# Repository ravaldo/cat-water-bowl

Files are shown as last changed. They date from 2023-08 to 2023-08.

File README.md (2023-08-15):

# Auto-filling pet water bowl

As a (former) cat owner for many years, this project arose from of my increasing dislike with the time it took to clean and maintain the pet [drinking fountain](https://i.imgur.com/fLEMcdn.jpg) I had. I wanted to return to a standard water bowl again and have it automatically filled with water:
* quick to clean
* no need to purchase filters
* smaller volumes of water meant fewer worries of water stagnating
* push notifications sent to my phone
  
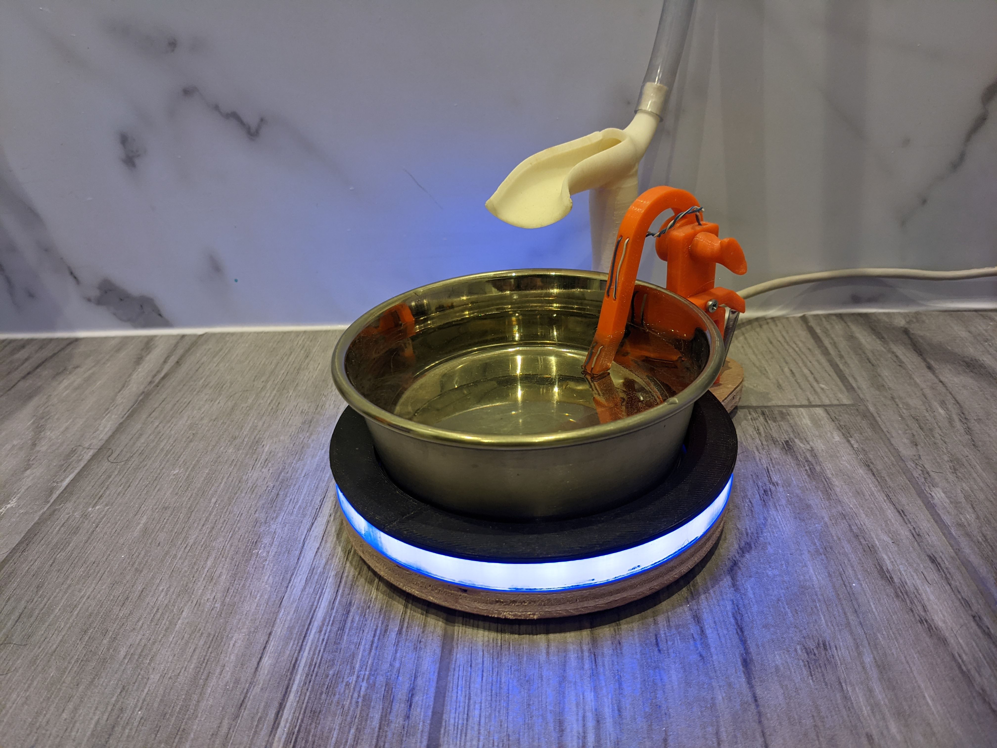
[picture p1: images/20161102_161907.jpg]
3d printed


## CAD / 3d Printing
The Fusion 360 file is included. I printed the spout in ABS in three parts so I could solvent weld them together and then vapour smooth them to be water proof. The light ring was printed in a transparent PLA. While the base could be printed (assuming your print bed is large enough) I opted to make it out of plywood and a 1:1 paper template is included.

## Hardware
|quantity|parts|
|:-:|-|
|1|Arduino Nano|
|2|NRF24L01|
|1|N-Channel Mosfet (SUP75N06-08)|
|1|Flyback Diode (1N4004)|
|3|NPN Transistors (BC548)|
|1|5V Voltage Regulator (LD117AV50)|
|1|3.3V Voltage Regulator (LD117AV33)|
|1|12V RGB LED strip segment|
|6|capacitors|
|6|resistors|
|2|RJ45 breakout boards or keystone jacks|
|1|DC Barrel Jack|
|1|12V Power Supply|
|1|12V Solenoid Valve (!NORMALLY CLOSED!)|
|1|15mm equal isolating tee|
|1|15mm x 1/4" compression straight adaptor|
|1|10mm barbed fitting to 1/4" BSP|
|1m|3/8" ID, 1/2" OD Hose|
|1|small tension spring|
|2|M5 nuts
|2|M5 pan head screws

It's worth mentioning that I made this project around 2012 which is why the NRF24L01 module is used for communication (the first ESP8266 was released a few years later). If I were redeploying this again today I would opt for a single ESP32 board and set it up for [MQTT](https://mqtt.org/).

Like most UK bathrooms I didn't have a convenient socket nearby, so, while the fountain resided next to my bathroom sink (plumbed into the cold water line), the circuit and power supply were in an adjacent room; the fountain was connected by an ethernet cable (hence the RJ45 adapters) and the solenoid valve was connected using 2 core speaker wire.

## Code
The arduino sketch is set up as a [finite-state machine](https://en.wikipedia.org/wiki/Finite-state_machine) with two primary inputs; one to detect if the bowl is present and another to detect if the bowl contains water. Two secondary inputs are available for setup and testing; one allows to you set the "water filling time" at the fountain and the other is used to test connectivity between the NRF24 modules.

Short demo video [HERE](https://youtu.be/1sBqBGg-HPs).

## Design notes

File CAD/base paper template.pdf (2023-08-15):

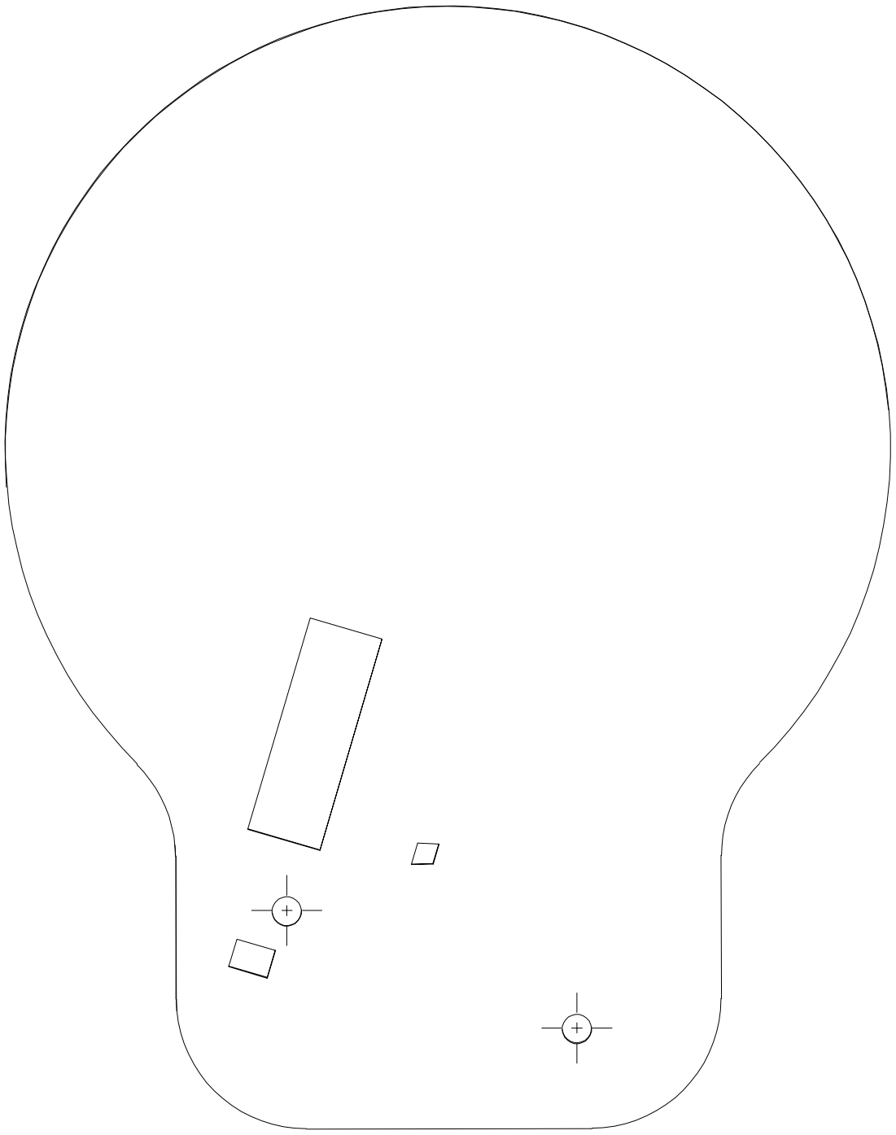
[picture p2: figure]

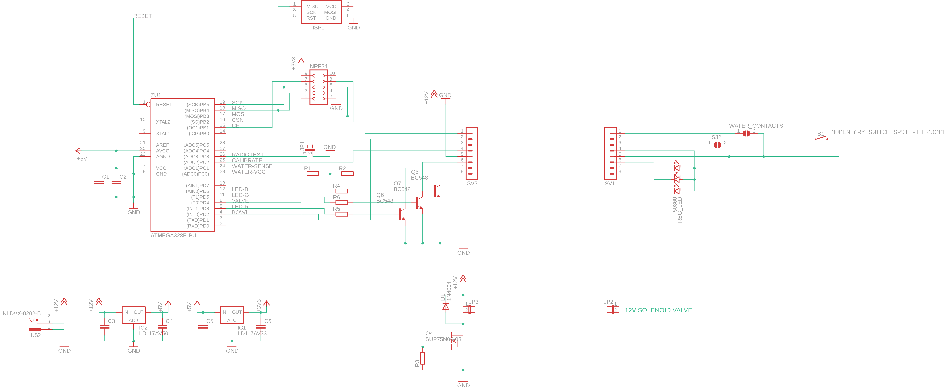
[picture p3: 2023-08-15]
circuit/schematic.png

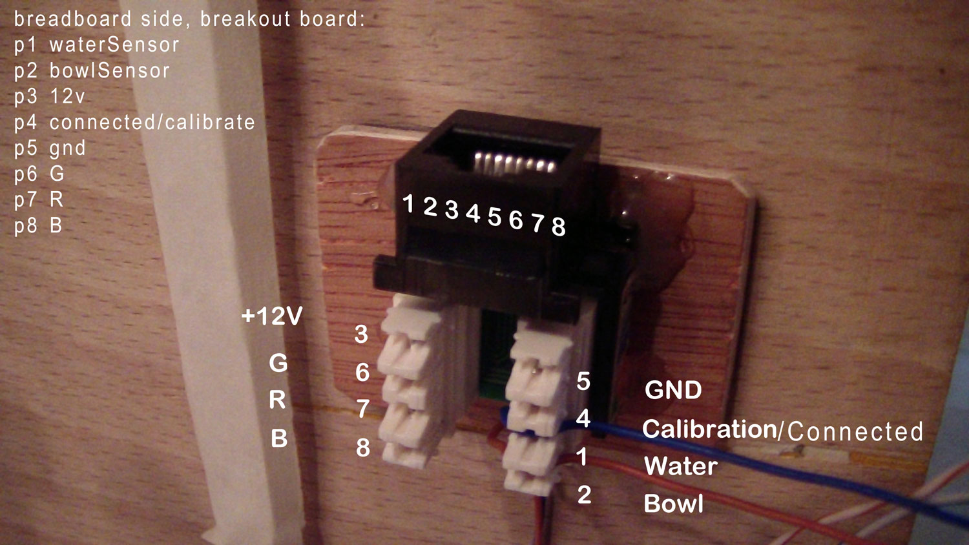
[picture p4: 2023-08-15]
circuit/ethernet pinout.jpg

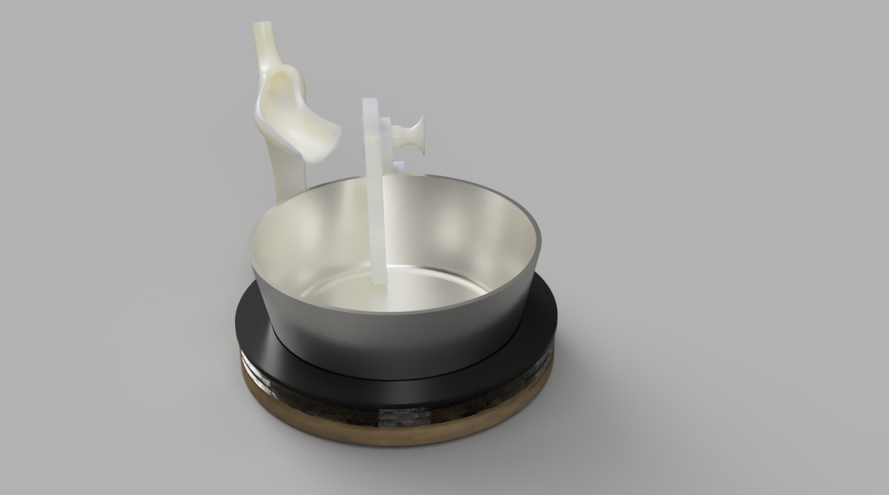
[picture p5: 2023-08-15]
CAD/render.png

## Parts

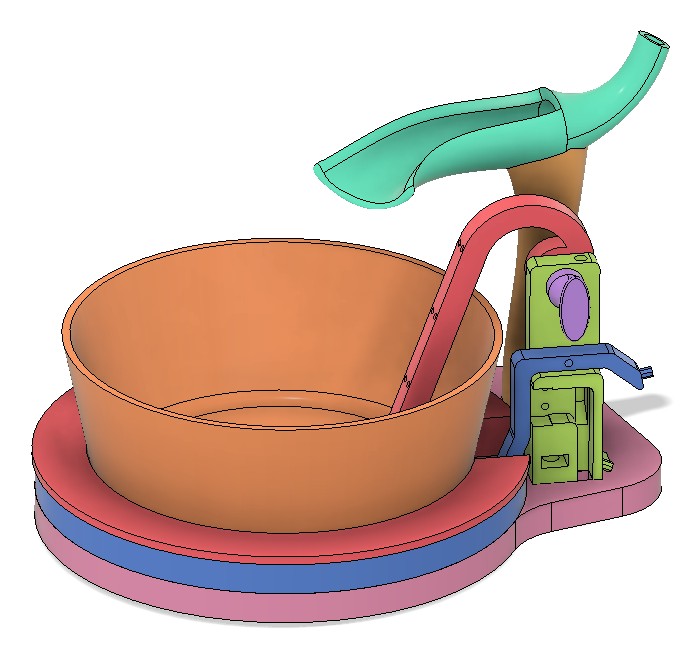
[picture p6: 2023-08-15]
CAD/component view.jpg

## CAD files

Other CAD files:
CAD/water bowl.f3d

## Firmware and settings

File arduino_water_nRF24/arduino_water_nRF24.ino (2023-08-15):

#include <SPI.h>
#include "RF24.h"
#include "RF24Network.h"
#include "my_vars.h"

////////////////////////////////////////////

#define secs *1000UL
#define mins *60 secs
#define hrs *60 mins

unsigned long bowlWait = 5 mins;          // time to wait for bowl to return
unsigned long evaporationWait = 25 mins;  // time to wait for water to evaporate before filling
unsigned long waterSampleWait = 5 mins;   // duration between taking water samples
unsigned long waterFillingTime = 25 secs; // changed in CALIBRATING mode
const unsigned long maxTimeOn = 30 secs;  // max time the valve will be on in a single WATERFILLING event
const unsigned long minTimeOn = 10 secs;  // min time the valve will be on in a single WATERFILLING event
const unsigned long expFillGap = 6 hrs;   // min 6hrs expected between fills, for warning purposes
const unsigned long debugPrintWait = 1 secs;   // time to wait to output debug msgs
const unsigned long armLoweringWait = 10 secs; // time to wait for sensor arm to be lowered

const int ledR = 7;
const int ledG = 5;
const int ledB = 6;
const int bowlSensor = 2; // INT0 is pin2
const int valve = 4;
const int waterVcc = A0;
const int waterSensor = A1;
const int calibrationPin = A2;
const int radioTestPin = A3;
const int connectedLed = A4;
const int connectedPin = 3;
const int debugSelect = 8;
const int CE = 9;
const int CSN = 10;
// unused pins A5, A6, A7
// nano PWM pins: 3, 5, 6, 9, 10, 11
// nRF24L01 set up on the nano's SPI bus... 9-CE, 10-CSN, 11-MO, 12-MI, 13-SCK

const char msg_FOUNTAINRESET[] = "fountain reset";
const char msg_READY[] = "fountain ready";
const char msg_BOWLREMOVED[] = "bowl removed";
const char msg_BOWLMISSING[] = "bowl missing > 5mins";
const char msg_BOWLREPLACED[] = "bowl replaced";
const char msg_BOWLEMPTY[] = "bowl empty";
const char msg_FILLED[] = "bowl filled";
const char msg_FILLEDTOOSOON[] = "filled again too soon";
const char msg_CHECKWATERSENSOR[] = "check water sensor";
const char msg_CALIBRATED[] = "fill time calibrated";
const char msg_RADIOTEST[] = "radio test";
const char msg_DISCONNECTED[] = "fountain disconnected";
const char msg_CONNECTED[] = "fountain connected";

boolean msgDisconnectedSent = false;
boolean msgRemovedSent = false;
boolean msgMissingSent = false;
boolean msgFilledTooSoonSent = false;
boolean msgErrorSent = false;

volatile State state;
volatile unsigned long timeStamp = 0;     
volatile unsigned long lastInterrupt = 0;
volatile int countInterrupts = 0;
unsigned long lastFillTime = 0;           // time since the bowl was last filled
unsigned long lastWaterSampleTime = 0;    // time since the water was last sampled
unsigned long lastDebugOutput = 0;        // time since the debug msg was last printed

const int nodeID = 1;  // unique nodes required for each project
RF24 radio(CE,CSN);
RF24Network network(radio);

////////////////////////////////////////////

void setup() {
  Serial.begin(57600);
  Serial.println("System started");

  SPI.begin();
  radio.begin();
  network.begin(90, nodeID);

  delay(100);
  pinMode(valve, OUTPUT);
  pinMode(waterVcc, OUTPUT);
  digitalWrite(valve, LOW); // make sure valve is off
  digitalWrite(waterVcc, LOW);

  pinMode(ledR, OUTPUT);
  pinMode(ledG, OUTPUT);
  pinMode(ledB, OUTPUT);
  pinMode(connectedLed, OUTPUT);
  pinMode(connectedPin, INPUT_PULLUP);
  pinMode(calibrationPin, INPUT_PULLUP);
  pinMode(bowlSensor, INPUT_PULLUP);
  pinMode(radioTestPin, INPUT_PULLUP);
  pinMode(debugSelect, INPUT_PULLUP);
  pinMode(waterSensor, INPUT); // using external 1Mohm pullup

  attachInterrupt(0, whereIsMyBowl, CHANGE); // INT0 is pin2
  attachInterrupt(1, whereIsMyBowl, CHANGE); // INT1 is pin3
  
  transmit(msg_FOUNTAINRESET, sizeof(msg_FOUNTAINRESET));
  digitalWrite(connectedLed, HIGH);
  if (!isFountainConnected() || !isBowlPresent())
    whereIsMyBowl();
  else                   // could just set it to start from DISCONNECTED
    setState(ARMWAIT);   // but doing this avoids the extra prints & emails being sent
  Serial.println("Setup finished");
}

////////////////////////////////////////////

void loop() {
  
  if (digitalRead(debugSelect) == LOW) {
    if (uint32_t(millis() - lastDebugOutput) > debugPrintWait)
      printStatus(); // particularly handy to check the waterSensor sensitivity
  }

  switch(state) {

    case DISCONNECTED: {
      setColour(BLACK);
      digitalWrite(valve, LOW);
      digitalWrite(waterVcc, LOW);
      digitalWrite(connectedLed, LOW);
      if (!msgDisconnectedSent) { // limit msgs to one per event
          transmit(msg_DISCONNECTED, sizeof(msg_DISCONNECTED));
          msgDisconnectedSent = true;
      }
      if (isFountainConnected()) {
        delay(100); // guard against accidental presses
        if (isFountainConnected) { // fountain definitely reconnected
          transmit(msg_CONNECTED, sizeof(msg_CONNECTED));
          msgDisconnectedSent = false; // reset
          digitalWrite(connectedLed, HIGH);
          setState(BOWLMISSING);
        }
      }
      break;
    }    
    
    case BOWLMISSING: {
      digitalWrite(valve, LOW);
      digitalWrite(waterVcc, LOW);
      unsigned long elapsedTime = millis() - timeStamp;
      if (elapsedTime <= bowlWait) {
        setColour(YELLOW);
        if (!msgRemovedSent) { // limit msgs to one per event
          transmit(msg_BOWLREMOVED, sizeof(msg_BOWLREMOVED));
          msgRemovedSent = true;
        }
      }
      if (elapsedTime > bowlWait) {
        setColour(RED);
        if (!msgMissingSent) { // limit msgs to one per event
          transmit(msg_BOWLMISSING, sizeof(msg_BOWLMISSING));
          msgMissingSent = true;
        }
      }
      if (isBowlPresent()) {
        delay(100); // guard against accidental presses
        if (isBowlPresent()) { // bowl definitely back
          transmit(msg_BOWLREPLACED, sizeof(msg_BOWLREPLACED));
          msgRemovedSent = false; // reset
          msgMissingSent = false; // reset
          setState(ARMWAIT);
        }
      }
      break;
    }

    case ARMWAIT: {
      // the bowl has just been replaced and it's likely empty...
      // lets not wait for evaporationWait, instead
      // wait X seconds to allow the arm to be lowered and then check water level
      setColour(WHITE);
      if (uint32_t(millis() - timeStamp) > armLoweringWait) {
        if (isWaterEmpty() && isBowlPresent()) {
          transmit(msg_BOWLEMPTY, sizeof(msg_BOWLEMPTY));
          setState(WATERFILLING);
        }
        else {
          transmit(msg_READY, sizeof(msg_READY));
          setState(READY);
        }
      }
      break;
    }
    
    case WATEREMPTY: {
      setColour(MAGENTA);
      if (!isWaterEmpty()) {
        transmit(msg_READY, sizeof(msg_READY));
        setState(READY);
        break;
      }
      if (uint32_t(millis() - lastFillTime) < expFillGap) {
        if (!msgFilledTooSoonSent) { // limit msgs to one per event
          transmit(msg_FILLEDTOOSOON, sizeof(msg_FILLEDTOOSOON));
          msgFilledTooSoonSent = true;
        }
      }
      if (uint32_t(millis() - timeStamp) >= evaporationWait) {
        msgFilledTooSoonSent = false; // reset
        setState(WATERFILLING);
      }
      break;
    }
    
    case WATERFILLING: {
      setColour(CYAN);
      if (uint32_t(millis() - timeStamp) < waterFillingTime)
        digitalWrite(valve, HIGH);
      else {
        digitalWrite(valve, LOW);
        lastFillTime = millis();
        timeStamp = millis();
        transmit(msg_FILLED, sizeof(msg_FILLED));
        if (isWaterEmpty())  // check the sensor is picking up the fresh water
          setState(ERRORS);
        else {
          transmit(msg_READY, sizeof(msg_READY));;
          setState(READY);
        }
      }
      break;
    }
    
    case CALIBRATING: {
      setColour(GREEN);
      digitalWrite(valve, HIGH);
      unsigned long elapsedTime = millis() - timeStamp;
      if (digitalRead(calibrationPin)) {    // if pin gone back to high
        delay(100);
        if (digitalRead(calibrationPin)) {  // debounce
          waterFillingTime = elapsedTime;
          if (elapsedTime > maxTimeOn)      // ensure we can't set it to overfill
            waterFillingTime = maxTimeOn;        
          if (elapsedTime < minTimeOn)      // ensure we can't set it too small
              waterFillingTime = minTimeOn;
          digitalWrite(valve, LOW);
          lastFillTime = millis();
          transmit(msg_CALIBRATED, sizeof(msg_CALIBRATED));
          setState(READY);
        }
      }
      break;
    }
    
    case RADIOTEST: {
      if (!transmit(msg_RADIOTEST, sizeof(msg_RADIOTEST))) {
        setColour(ORANGE);
        delay(500);
        setColour(PURPLE);
        delay(500);
      }
      else {
        setColour(ORANGE);
        delay(500);
        setColour(GREEN);
        delay(500);
      }
      if (digitalRead(radioTestPin)) // pin gone back to high
        state = READY; // set it directly so it doesn't print or reset the timestamp
      break;
    }
    
    case READY: {
      digitalWrite(valve, LOW);
      digitalWrite(waterVcc, LOW);
      setColour(BLUE);
      if (!isFountainConnected()) {
        Serial.println("  -- WE CAUGHT A DISCONNECTED EVENT NOT USING THE INTERRUPT.");
        setState(DISCONNECTED);
        break;
      }
      if (!isBowlPresent()) {
        Serial.println("  -- WE CAUGHT A BOWLMISSING EVENT NOT USING THE INTERRUPT.");
        setState(BOWLMISSING);
        break;
      }
      if (isCalibrating()) {
        setState(CALIBRATING);
        break;
      }
      if (isRadioTesting()) {
        state = RADIOTEST; // set it directly so it doesn't print or reset the timestamp
        break;
      }
      if (uint32_t(millis() - lastWaterSampleTime) > waterSampleWait) {
        lastWaterSampleTime = millis();
        if (isWaterEmpty()) {
          transmit(msg_BOWLEMPTY, sizeof(msg_BOWLEMPTY));
          setState(WATEREMPTY);
          break;
        }
      }
      break;
    }
    
    case ERRORS: {
      if (!msgErrorSent) {
        detachInterrupt(0);
        detachInterrupt(1);
        transmit(msg_CHECKWATERSENSOR, sizeof(msg_CHECKWATERSENSOR));
        msgErrorSent = true;
      }
      delay(500);
      setColour(RED);
      delay(500);
      setColour(BLACK);
      // reaching this state indicates the water was filled and the sensor didn't pick it up
      // possible cause 1; the water sensor was left raised up
      // possible cause 2; the water sensor wires have corroded and need replaced
      // need to reset the power if we reach this state
    }
    
    default:
      break;
  }// end of switch
}// end of loop

// interrupt routine
void whereIsMyBowl() {
  digitalWrite(valve, LOW);
  digitalWrite(waterVcc, LOW);
  
  if ((millis() - lastInterrupt) > 100) {
    if (!isFountainConnected())
      state = DISCONNECTED;
    else
      state = BOWLMISSING;

    timeStamp = millis();
    lastInterrupt = millis();
    countInterrupts++;
  }  
  // putting in the debounce logic has the effect of reducing multiple triggering
  // but the valve output isn't always forced to low as we would expect
  // therefore; copied the digitalWrites up to the switch case which ensures they are turned off
  // ... left them in this function anyway since it can't hurt
}

void setState(State s) {
  state = s;
  timeStamp = millis();
  printStatus();
}

////////////////////////////////////////////

boolean isBowlPresent() {
  return digitalRead(bowlSensor) == LOW ? true : false;
  // bowl pin pulled high by default
  // bowl switch is wired "normally open"
  // when bowl is present; switch is made; pin is low
  // when bowl is removed; switch is broken; pin is high
}

boolean isFountainConnected() {
  return digitalRead(connectedPin) == LOW ? true : false;
}

boolean isWaterEmpty() {
  int sample = getWaterSample();
  return sample < 150 ? false : true;
  // water pin pulled high temporarily using another outout pin and external resistor
  // water present; line is shorted; pin is pulled towards ground
}

boolean isCalibrating() {
  return digitalRead(calibrationPin) == LOW ? true : false;
}

boolean isRadioTesting() {
  return digitalRead(radioTestPin) == LOW ? true : false;
}

int getWaterSample(){
  digitalWrite(waterVcc, HIGH);
  delay(5);
  int sensorValue = analogRead(waterSensor);
  delay(5);
  digitalWrite(waterVcc, LOW);
  return sensorValue;
}

void setColour(const int colour[]){
  analogWrite(ledR, colour[0]);
  analogWrite(ledG, colour[1]);
  analogWrite(ledB, colour[2]);
}

void printStatus() {
  lastDebugOutput = millis();
  Serial.print("state: ");
  switch(state) {
    case BOWLMISSING:   Serial.print("BOWLMISSING"); break;
    case WATEREMPTY:    Serial.print("WATEREMPTY"); break;
    case WATERFILLING:  Serial.print("WATERFILLING"); break;
    case ARMWAIT:       Serial.print("ARMWAIT"); break;
    case READY:         Serial.print("READY"); break;
    case CALIBRATING:   Serial.print("CALIBRATING"); break;
    case RADIOTEST:     Serial.print("RADIOTEST"); break;
    case DISCONNECTED:  Serial.print("DISCONNECTED"); break;
    case ERRORS:        Serial.print("ERRORS"); break;
  }
  Serial.print("  ||  waterSensor: ");
  Serial.print(getWaterSample(), DEC);
  Serial.print("  ||  waterFillingTime: ");
  Serial.print(waterFillingTime, DEC);
  Serial.print("  ||  lastFillTime: ");
  Serial.print(lastFillTime, DEC);
  Serial.print("  ||  interrupts: ");
  Serial.print(countInterrupts, DEC);
  Serial.print("  ||  bowlSensor: ");
  Serial.print(digitalRead(bowlSensor));
  Serial.print("  ||  connectedPin: ");
  Serial.print(digitalRead(connectedPin));
  Serial.print("  ||  timeStamp: ");
  Serial.println(timeStamp, DEC);
}

bool transmit(const char msg[], int msgsize) {
  network.update();
  RF24NetworkHeader header(0, 'W');
  
  int count = 1;
  bool ok = false;
  while (count <= 3 && !ok) {
    Serial.print("Sending: ");
    Serial.print(msg);
    ok = network.write(header, msg, msgsize);
    if (ok)
      Serial.println(" ... successfull! ");
    else
      Serial.println(" ... failed!");
    count++;
  }
  return ok;
}

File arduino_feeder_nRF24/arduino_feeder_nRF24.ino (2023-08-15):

#include <SPI.h>
#include "HX711.h"
#include "RF24.h"
#include "RF24Network.h"

#define secs *1000UL
#define mins *60 secs
#define hrs *60 mins
#define day *24 hrs

const int motorPin = 5;
const int foodSensor = 6;
const int foodLight = 7;
const int radioTestPin = 8;
const int CE = 9;
const int CSN = 10;
// HX711_SCK 2 , HX711_DT 3
// nRF24L01 set up on the nano's SPI bus... 9-CE, 10-CSN, 11-MO, 12-MI, 13-SCK

const char msg_RESET[] = "reset";
const char msg_READY[] = "ready";
const char msg_FILLED[] = "bowl filled";
const char msg_NEAREMPTY[] = "near empty - top it up!";
const char msg_FAILEDFILL[] = "bowl was not filled after a minute; check food/blockage";
const char msg_RADIOTEST[] = "radio test";
const char msg_DEFAULTTIME[] = "default wait time elapsed without any msgs from server";

int defaultAmount = 30;  // grams
int currentWeight = 0;

unsigned long lastFeedTime = 0;
unsigned long lastSampleTime = 0;
unsigned long attemptTime = 60 secs;
unsigned long defaultWait = 1 day + 1 hrs;
unsigned long sampleWait = 5 mins;

const int nodeID = 2;  // unique nodes required for each project
RF24 radio(CE,CSN);
RF24Network network(radio);

/////////////////////////////////////////////////////////////////////////////

void setup(void) {
  Serial.begin(57600);
  Serial.println("Setup began");
  Init_Hx711();
  delay(3000);
  Get_Maopi();
  
  SPI.begin();
  radio.begin();
  network.begin(90, nodeID);
  
  pinMode(motorPin, OUTPUT);
  pinMode(foodSensor, INPUT);
  pinMode(foodLight, OUTPUT);
  pinMode(radioTestPin, INPUT_PULLUP);
  
  #ifdef DEBUG
    digitalWrite(motorPin, HIGH);
    delay(1000);
    digitalWrite(motorPin, LOW);
  #endif

  transmit(msg_RESET, sizeof(msg_RESET));
  Serial.println("s <weight>     set default output amount");
  Serial.println("g              get default output amount");
  Serial.println("o              output default amount");
  Serial.println("o <weight>     output the given amount");
  Serial.println("r              read sensor");
  Serial.println("c              clear sensor");
  Serial.println(">              drive screw forwards");
  Serial.println("<              drive screw backwards");
  Serial.print("System started. Current weight: ");
  Serial.println(Get_Weight());
}


void loop() {
  network.update();

  while (digitalRead(radioTestPin) == LOW) {
    if (transmit(msg_RADIOTEST, sizeof(msg_RADIOTEST)))
      Serial.println("radio test succeeded");
    else
      Serial.println("radio test failed");
    delay(1000);
  }

  // check how much has been eaten
  // TODO - add a delay to make sure we aren't reading when the scale is being pushed down
  if (uint32_t(millis() - lastSampleTime) > sampleWait) {
    int eaten = currentWeight - sensor();
    if (eaten >= 1) {
      char msg[40];
      sprintf(msg, "eaten %i, remaining %i", eaten, sensor());
      Serial.println(msg);
      transmit(msg, sizeof(msg));
    }
    lastSampleTime = millis();
  }
      
  // check if it needs topped up
  if (foodSensor == LOW) {
    Serial.println(msg_NEAREMPTY);
    transmit(msg_NEAREMPTY, sizeof(msg_NEAREMPTY));
  }

  if (uint32_t(millis() - lastFeedTime) > defaultWait) {
    Serial.println(msg_DEFAULTTIME);
    transmit(msg_DEFAULTTIME, sizeof(msg_DEFAULTTIME));
    output(defaultAmount);
  }
  
  checkSerialForInput();
  checkRadioForInput();
}// end of loop

/////////////////////////////////////////////////////////////////////////////

void output(int amount) {
  char msg[80];
  sprintf(msg, "outputting %i grams", amount);
  Serial.println(msg);
  transmit(msg, sizeof(msg));

  unsigned long startingTime = millis();
  int startingWeight = sensor();
  while (sensor() < (startingWeight + amount)) {
    digitalWrite(motorPin, HIGH);
    delay(600);
    digitalWrite(motorPin, LOW);
    delay(200);
    printWeight();
    //timeout
    if (uint32_t(millis() - startingTime) > attemptTime) {
      Serial.println(msg_FAILEDFILL);
      transmit(msg_FAILEDFILL, sizeof(msg_FAILEDFILL));
      break;
    }
  }
  delay(1000); // let the kibble settle
  printWeight();
  currentWeight = sensor();
  sprintf(msg, "startingWeight: %i || outputAmount: %i || target: %i || actual: %i", startingWeight, amount, startingWeight+amount, currentWeight);
  Serial.println(msg);
  transmit(msg, sizeof(msg));
}

void printWeight() {
  Serial.print("Current weight: ");
  Serial.println((int)Get_Weight());
}

int sensor() {
  return (int)Get_Weight(); // needs a cast as Get_Weight() returns unsigned int
}

void checkSerialForInput() {
  String s = "";
  while(Serial.available() > 0) {
    delay(20);
    s.concat(char(Serial.read()));
  }
  if (s != "")
    processInput(s);
}

void checkRadioForInput() {
  String s = "";
  if (network.available()) {
    delay(50);
    RF24NetworkHeader header;
    network.peek(header);
    if(header.type == 'F') {
      char msg[50];
      network.read(header, &msg, 50);
      s = String(msg);
      //Serial.print("received via radio: ");
      //Serial.println(s);
    }
  }
  if (s != "")
    processInput(s.substring(s.indexOf(" ")+1)); // strip the FEEDER prefix
}

void processInput(String s) {
  switch(s.charAt(0)) {
    case 's': {
      defaultAmount = (s.substring(s.indexOf(" "))).toInt();
    } // fall through
    case 'g': {
      char msg[50];
      sprintf(msg, "default amount set to: %i", defaultAmount);
      Serial.println(msg);
      transmit(msg, sizeof(msg));
      break;
    }
    case 'o': {
      if (s.length() == 1)
        output(defaultAmount);
      else
        output(  (s.substring(s.indexOf(" "))).toInt()  );
      break;
    }
    case 'r': {
      char msg[50];
      sprintf(msg, "current weight:  %i", sensor());
      Serial.println(msg);
      transmit(msg, sizeof(msg));
      break;
    }
    case 'c': {
      Get_Maopi();
      break;
    }
    case '>': {
      digitalWrite(motorPin, HIGH);
      delay(600);
      break;
    }
    case '<': {
      digitalWrite(motorPin, HIGH);
      delay(600);
      break;
    }        
    default:
      break;
  }
}

bool transmit(const char msg[], int msgsize) {
  network.update();
  RF24NetworkHeader header(0, 'F');
  
  int count = 1;
  bool ok = false;
  while (count <= 3 && !ok) {
    Serial.print("Sending: ");
    Serial.print(msg);
    ok = network.write(header, msg, msgsize);
    if (ok)
      Serial.println(" ... successfull! ");
    else
      Serial.println(" ... failed!");
    count++;
  }
  return ok;
}
